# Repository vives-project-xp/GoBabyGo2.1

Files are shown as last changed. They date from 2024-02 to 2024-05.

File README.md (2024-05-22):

# GoBabyGo2.1

## About

Go Baby Go 2.1 is an innovative project that aims to enhance the mobility and independence of children with disabilities.
This project was created as part of the Project Experience course at [VIVES University of Applied Sciences](https://www.vives.be/en), in collaboration with the Ergotherapy program. This project focuses on adapting mini-cars to meet the specific needs of these children.
The main goal of this project is to create a working product out of the previous proof of concept [GoBabyGo2.0](https://github.com/vives-project-xp/GoBabyGo2.0), where the functions of the steeringweel and the gaspedal are replaced by a joystick.
By creating adaptable vehicle kits and comprehensive instructions, the project strives to empower caregivers and non-technical individuals to customize cars for children with ease.

## The team

- [Alberiek Depreytere](https://github.com/AlberiekDepreytere): Supervision, assembly, architectural design,...
- [Vic Verbiest](https://github.com/Vic-Verbiest): methodologie, bestellingen, 3d prints
- [Lynn Delaere](https://github.com/LynnDelaere): Maintain documentation and support developers

## Features

- Assembly kit development
- Comprehensive manual
- Implementing joystick as steering
- Standalone with interference from controller

## How it works

The project focusses on developing a user-friendly assembly kit with easy to follow instructions for converting standard mini-cars into accessible vehicles for children with disabilities. The function of the steering wheel and accelerator pedals are replaced by a joystick.
The assembly kit comes with easy to follow instructions so the assembly kit can be made and added to the package of the car. Every car comes then with a conversion manual so the assembly kit can easily be installed on the car. The assembly kit is engineered with user-friendly design principles, ensuring accessibility for individuals without prior experience in electronics.

## Project status

The ride-on car has been successfully converted to a ride-on car with a joystick, a guide on how to make the assembly kit has been made and an installation manual had been written out.

## Documentation

The documentation folder contains an [assembly kit](/Documentation/Manuals/Handleiding%20ombouwkit.md) and an [installation manual](/Documentation/Manuals/Installatie%20ombouwkit.md) to convert a ride-on car.

//Last updatet 13/05/2024 09:00 CET

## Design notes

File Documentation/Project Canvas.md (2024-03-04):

# Project Canvas

## Purpose and goal

Make an assembly kit for a ride on car with a joystick.

## Scope

In this project, we need to modify a ride-on car to utilize a joystick instead of a steering wheel. This includes providing an easy-to-follow manual so that everybody can convert the ride-on car if necessary.

## Succes Criteria

This project will be a succes if we can create an easy assembly kit to modify the ride-on car.

## Milestones

- Week 1-3: developing concept and order list
- Week 4-6: devoloping a prototype
- Week 7-10: final product/ proof of concept
- Week 11-12: debugging and optimizing
- Week 13: presentation

## Actions

- Electronic diagram ride-on car
- Order list
- Testing joystick
- Measuring hardware
- 3D print to attach joystick
- Instruction manual
- Keeping GitHub up to date

## Team

- Alberiek Depreytere: Hardware engineer, Scrum master
- Vic Verbiest: ***AANVULLEN***
- Bavo Lezy: ***AANVULLEN***
- Lynn Delaere: Administration and communication

## Stakeholders

- Occupational therapy
- Project leader
- Parents of children with a disabilitie

## Users

Children with a disabilitie

## Resources

- Github repository
- Financial budget €175
- Lab equipment
- Input occupational therapy

## Constraints

- Financial budget
- Time (13 weeks)

## Risks

- Hardware not compatible with eachother
- Long-term absent team member
- Too complex conversion kit
- Loss of documentation

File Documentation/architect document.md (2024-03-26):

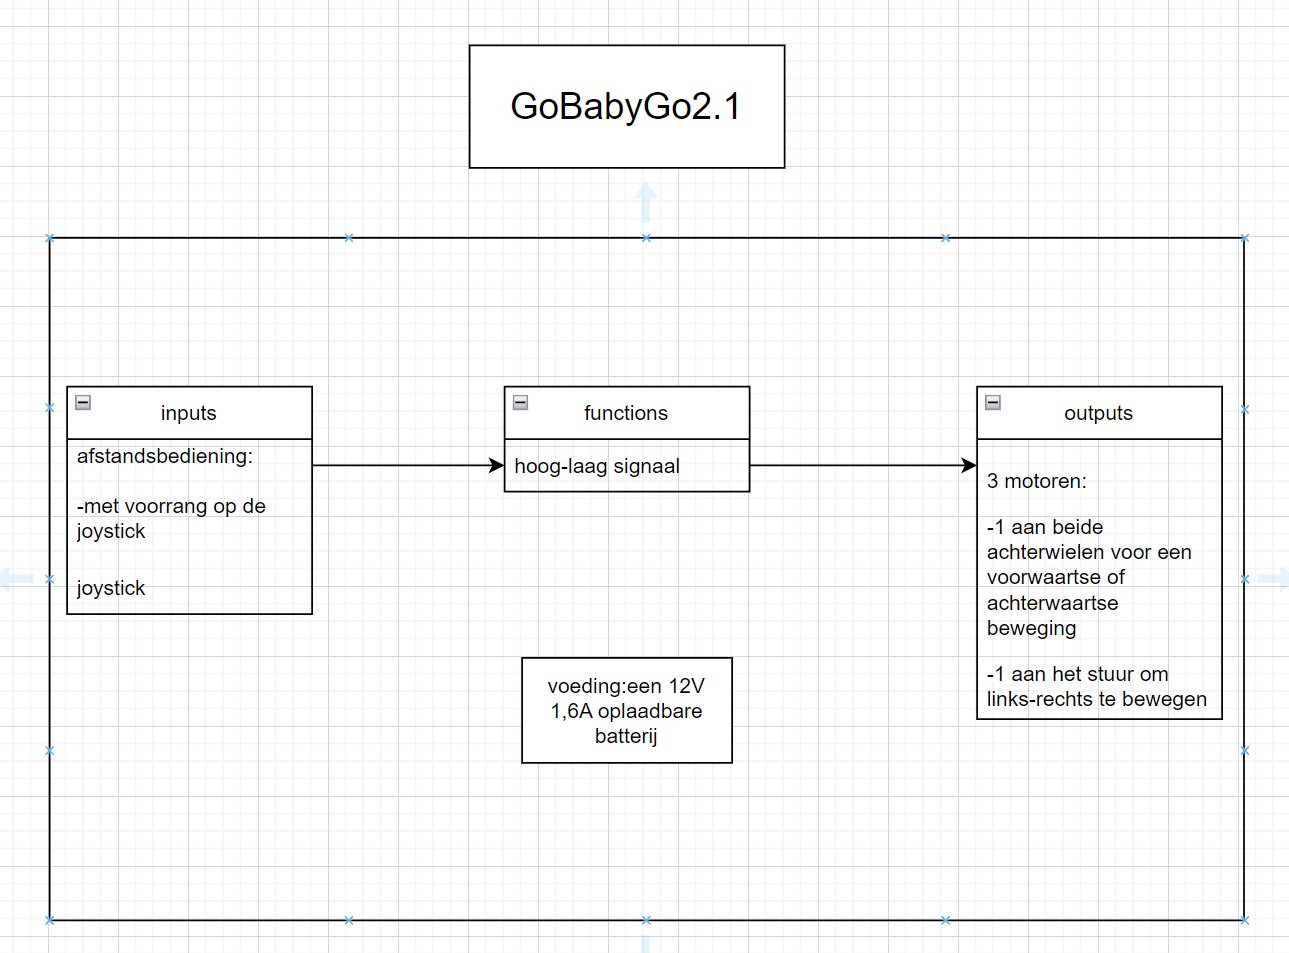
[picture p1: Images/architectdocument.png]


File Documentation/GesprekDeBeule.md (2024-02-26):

# Gesprek Isabelle De Beule
## Vragen Auto
Hebben jullie nog een originele auto zonder modificaties?
> Er Zijn nog 5 originele auto's Er zijn nog 5 originele auto’s aanwezig in campus Kortrijk in het zorglab. Er word een auto overgebracht zodat we een elektrisch schema kunnen opstellen aan de hand van een nieuwe auto. Aan de hand van een originele auto wordt eveneens de ombouwkit opgesteld.

Zijn de auto's allemaal van hetzelfde type?
> De auto’s die worden aangekocht zijn telkens van het merk Mercedes en hetzelfde model.

Waar werden de auto's aangekocht, welk model werd er aangekocht en wie is de fabrikant van de auto's?
> Bij [atoys](https://www.atoys.nl/webshop/verwacht/detail/1122/mercedes-benz-glc-63-elektrische-accu-auto-met-muziek-module-en-meer-1.html) worden de auto’s in bulk aangekocht, het model die telkens wordt besteld is de Mercedes Benz GLC 63

Wie heeft de modificaties uitgevoerd met de drukknop? Kunnen wij deze persoon in kwestie contacteren.
> De modificaties werden uitgevoerd door de studenten van zorgtechnologie onder begeleiding van de docent. Deseine Bert is de docent in kwestie. De voetpedaal werd enkel vervangen door een drukknop op het stuur.

## Vragen joystick
Hoeveel ruimte moet er vrijgehouden worden voor de plaatsing van de stoel?
>De joystick mag in de plaats komen waar het stuur zich nu bevind. Zo is er nog plaats om een aangepaste stoel te plaatsen indien nodig. Als de joystick te veel naar voor komt, is het moeilijker om een aangepaste stoel te plaatsen.

Hoe hoog mag de joystick komen?
>Doordat de joystick in de plaats komt van het stuur is dit geen probleem met hoogte. Maar veel hoger mag dit ook niet komen.

Moet dit een speciale joystick zijn of is deze die er momenteel inzit goed genoeg?
> Dit mag een standaard joystick zijn met niet te veel snufjes zodat de kindjes hierdoor geen extra prikkels krijgen.

Moet er nog iets van het dashboard werken?
> De muziek van het dashboard mag nog werken, er mag ook een optie in de kit aanwezig zijn dat dit er uit gehaald kan worden.
De startknop mag weg zodat de kindjes minder prikkels heeft en zich enkel kan focussen op de joystick.
De wielen aan de onderkant moeten blijven zitten zodat de ouders de auto nog kunnen voor uittrekken.
Er zijn enkele problemen met de batterij. Dit tijdens het opladen, de killswitch moet aan staan vooraleer de batterij kan opgeladen worden. Hier zullen we kijken of er een mogelijkheid is dat de batterij toch oplaad ongeacht de stand van de killswitch. Ook de levensduur van de batterij is een probleem, na 30-45 minuten rijden is de batterij plat. We houden de optie open om een zwaardere batterij te gebruiken die compatibel is met de schakeling die we zullen gebruiken.

## Extra info
Bert Deseine - docent elektronica in de opleiding zorgtech (handleiding)
Benjamin Van Der Smissen - docente project in de opleiding zorgtech
Sofie Vanmaercke - OH zorgtech

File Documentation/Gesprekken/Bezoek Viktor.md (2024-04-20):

# Bezoek Viktor 15/04/2024

Op 15/04/2024 kwam Viktor langs om een testrit uit te voeren met ons prototype. Viktor is het kindje die geselecteerd werd door ergotherapie en komt in aanmerking voor een ride on auto met joystick. Viktor rijd thuis regelmatig rond met een rolstoel met joystick dus bekend met het gebruik van een joystick.
Tijdens de testrit werd de werking van de ombouwkit geëvalueerd en de plaatsing van de joystick.
Over de werking van de schakeling is niets op aan te merken, de auto rijdt vooruit, achteruit, links en rechts wanneer de joystick deze richting geduwd wordt. De joystick is minder gevoelig dan de joystick dat Viktor gewent is. Dit komt deels doordat de constructie waarin de joystick zit wat wankel staat.
De werking van de schakeling is niets op aan te merken behalve dat de joystick die wordt gebruikt minder gevoelig is dan de joystick die Viktor gewoon is. Dit komt deels doordat de constructie van de 3D prints waar de joystick inzit niet stabiel staat. Dit wordt bekeken en de 3D prints worden aangepast waar nodig.
De plaatsing van de joystick werd zowel door de ouders van Viktor als ergotherapie goedgekeurd. In samenspraak met de ouders, ergotherapie en de projectcoaches werd er beslist om geen extra ondersteuning te voorzien voor Viktor zijn armpjes. Voor Viktor is dit een extra motivatie om zijn armpjes te strekken om zo goed de auto te besturen. Wel kan ergotherapie ervoor zorgen dat de zitschaal waar Viktor inzit wat naar voor geplaatst kan worden.

Hier zijn enkele foto's en een filmpje van Viktor in de auto.
<!--foto's toevoegen-->

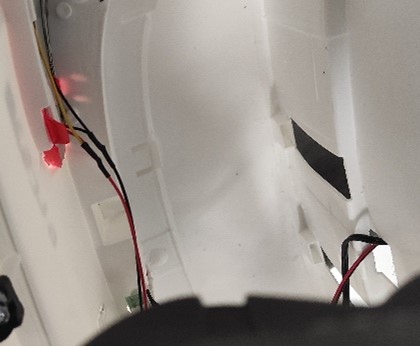
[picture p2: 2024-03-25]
Images/Draad_Doorsteken.jpg

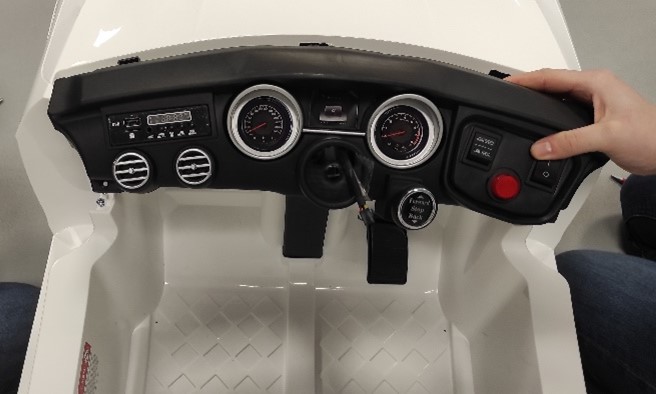
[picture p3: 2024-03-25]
Images/Dashboard_Afhalen.jpg

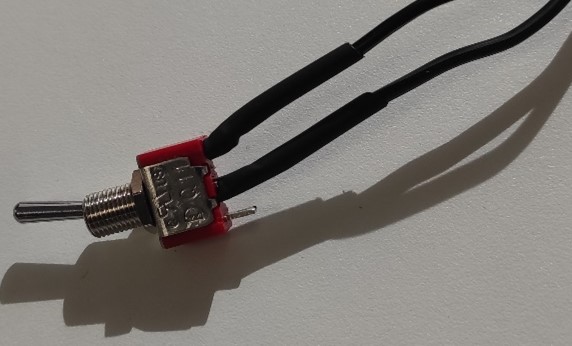
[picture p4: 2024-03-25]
Images/Killswitch_schakelaar.jpg

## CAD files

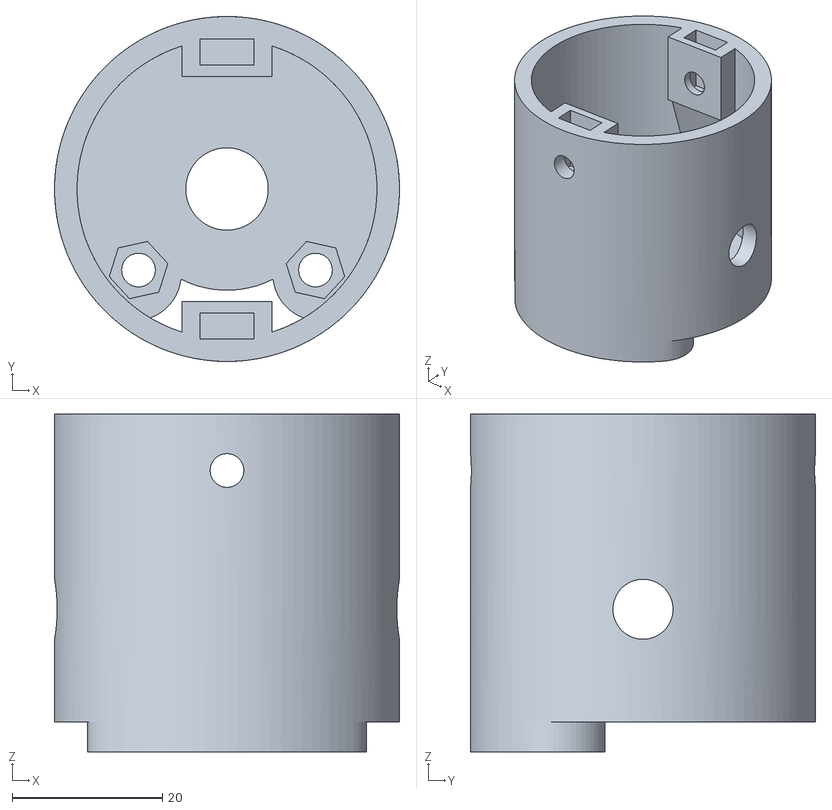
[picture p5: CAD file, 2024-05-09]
Documentation/Final Design 3D Prints/KoppelstukDashboard.stl
46.0 x 46.0 x 45.0

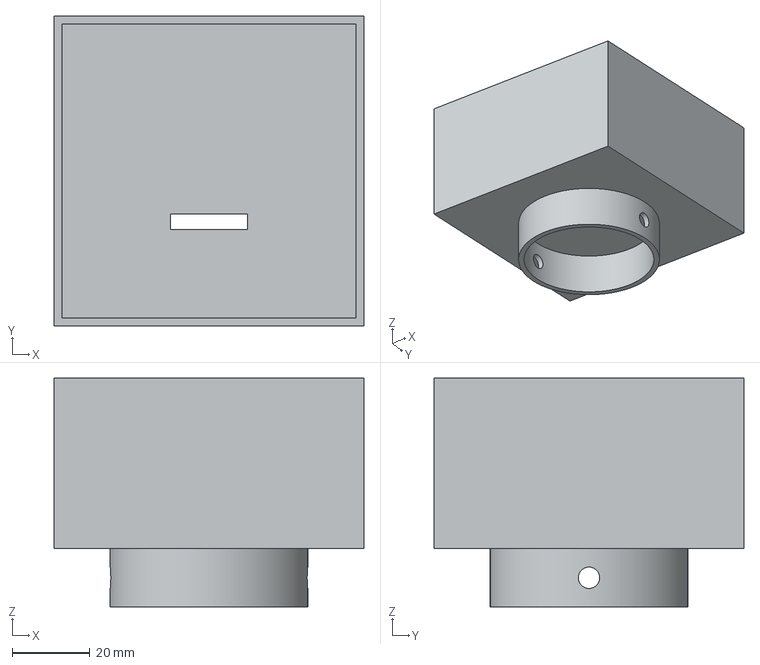
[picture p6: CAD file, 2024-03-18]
Documentation/Test Design 3D Prints/joystick.3mf
80.0 x 80.0 x 59.0 mm

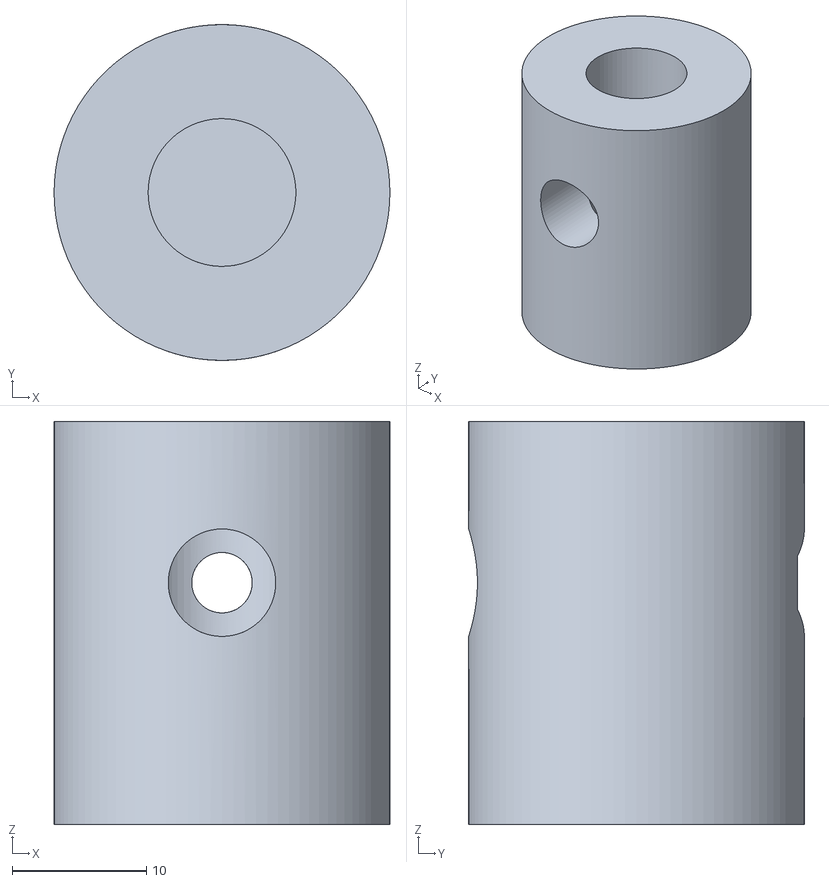
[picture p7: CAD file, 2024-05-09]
Documentation/Final Design 3D Prints/StuurStangHouder.stl
25.0 x 25.0 x 30.0

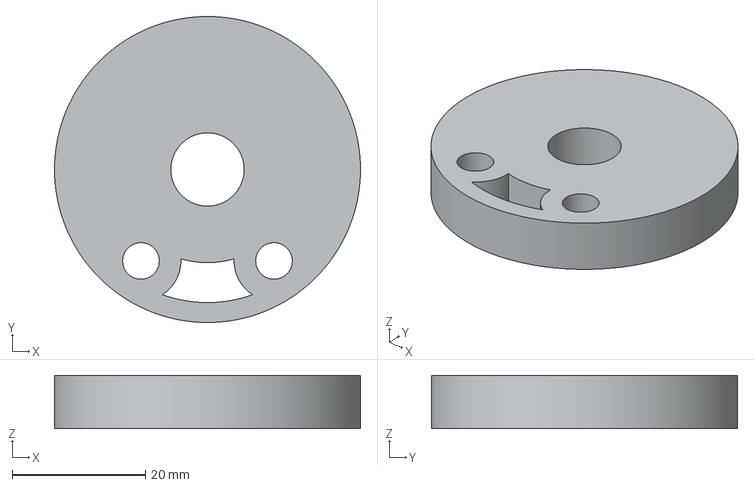
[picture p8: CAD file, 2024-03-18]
Documentation/Test Design 3D Prints/joystickhouderhouder.3mf
46.0 x 46.0 x 8.00 mm

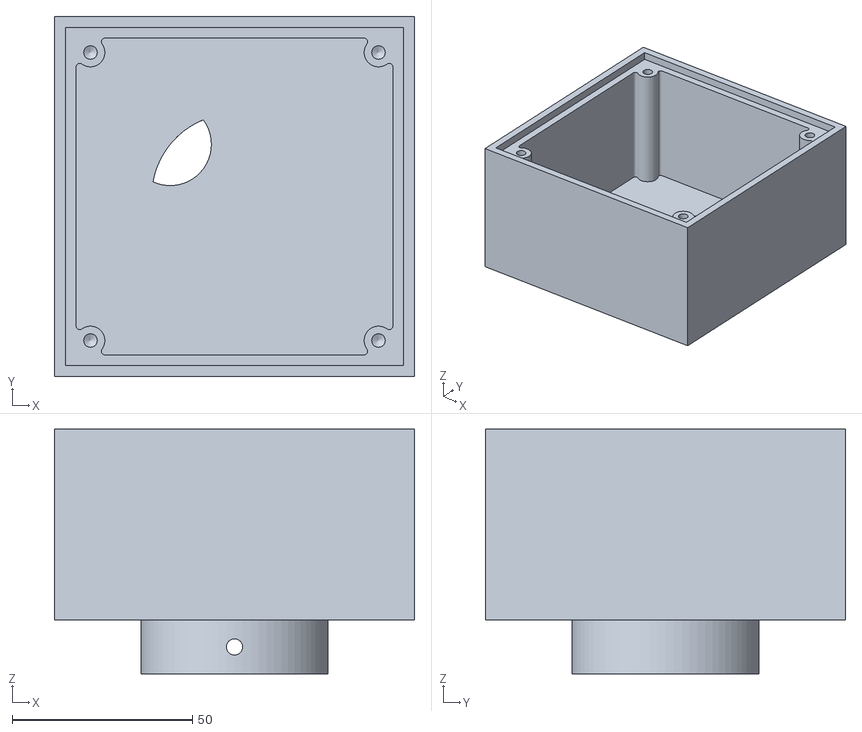
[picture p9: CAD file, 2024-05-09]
Documentation/Final Design 3D Prints/DoosJoystick.stl
100.0 x 100.0 x 68.0

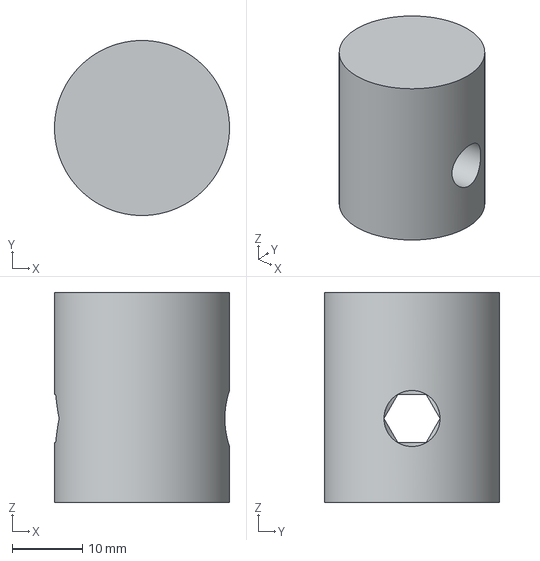
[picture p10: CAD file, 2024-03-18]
Documentation/Test Design 3D Prints/stanghouder.3mf
25.0 x 25.0 x 30.0 mm

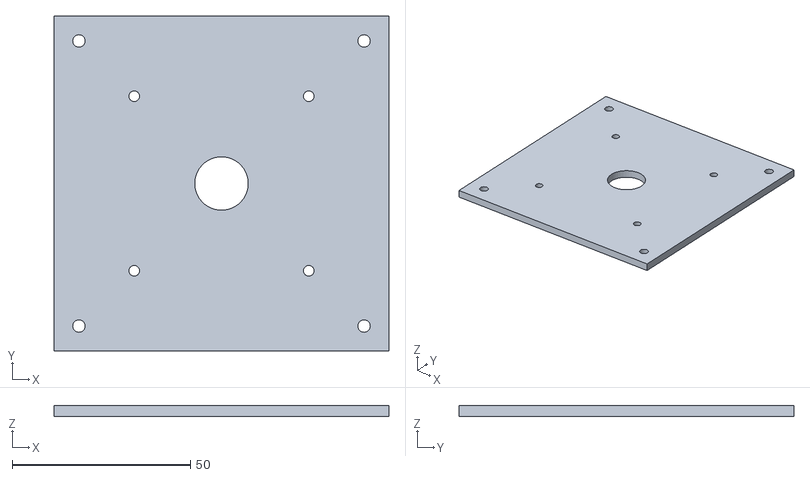
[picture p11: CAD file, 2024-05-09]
Documentation/Final Design 3D Prints/DekselDoos.stl
94.0 x 94.0 x 3.00

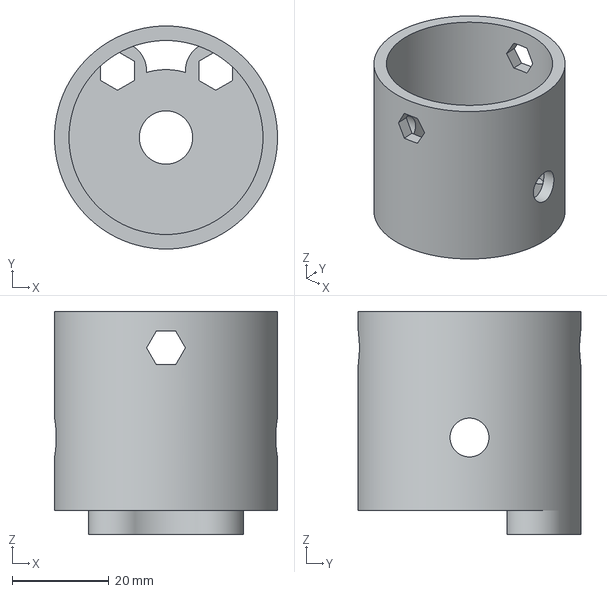
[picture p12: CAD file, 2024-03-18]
Documentation/Test Design 3D Prints/joystickhouder.3mf
46.0 x 46.0 x 46.0 mm

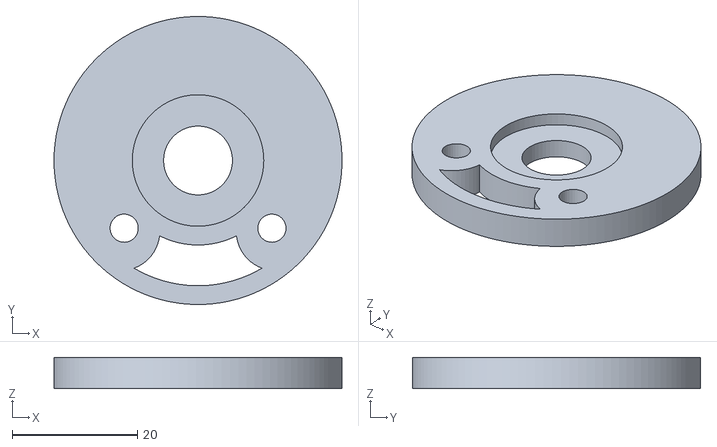
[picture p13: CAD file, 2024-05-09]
Documentation/Final Design 3D Prints/SpanStukDashboard.stl
46.0 x 46.0 x 5.00

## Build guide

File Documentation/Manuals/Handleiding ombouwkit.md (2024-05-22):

# Handleiding ombouwkit

## Inhoud

* [Opmerking](#opmerking)
* [Onderdelen](#onderdelen)
* [Materiaal](#materiaal)
* [Tools](#tools)
* [Handleiding](#handleiding)

## Opmerking

Deze ombouwkit is ontworpen voor een specifieke elektrische kinderauto van het type Mercedes-Benz GLC63, met productcode QLS5688-grey.

## Onderdelen

Hieronder vind je een lijst van de verschillende onderdelen die nodig zijn om de ombouwset te maken, de leveranciers van de onderdelen alsook een woordje uitleg over de onderdelen.

### Joystick

De joystick die gebruikt dient te worden is van het merkt Joy-IT, deze heeft 4 microschakelaars om de richting door te geven en springt automatisch terug naar de middenpositie. Deze is te verkrijgen bij de leverancier Conrad via deze [link](https://www.conrad.be/nl/p/joy-it-arcade-joystick-professional-8-invoerapparaat-geschikt-voor-arduino-banana-pi-cubieboard-pcduino-raspberry-p-1555268.html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).

### 3D onderdelen

Er zijn 5 verschillende 3D stukken nodig om de joystick vast te zetten op het dashboard van de auto, een doos om de joystick in weg te steken, een deksel om dit af te sluiten, een koppelstuk tussen het dashboard en de doos, een stuk die de stuurstang omhoog houdt en een stuk die dit alles vastzet aan de onderkant van het dashboard. In de map [3D-prints](../3D-prints/) vind je de verschillende onderdelen terug die zullen afgedrukt moeten worden.

### Motor driver

De links-rechtssturing wordt bepaald aan de hand van de motor die aanwezig is op de stuurstang in de auto. Via de driver wordt de richting van de motor bepaald deze is een L298N driver, te verkrijgen bij Otronic via deze [link](https://www.otronic.nl/nl/l298n-motor-driver-board-rood.html). [Datasheet L298N](DatasheetL298_H_Bridge.pdf)
De L298N is een dubbele H-brug-motordriver die de snelheid en de richting van twee DC-motoren tegelijk mogelijk maakt, in ons geval moeten we maar één motor aansturen. De module kan een DC-motor aansturen met een spanning tussen de 5 en 35V en een piekstroom van 2A.

Er zijn twee schroefklemmenblokken aanwezig respectievelijk voor motor A en motor B, een schroefklemblok voor de aarding, de Vcc voor de motor en een 5V-pin die zowel een ingang als een uitgang kan zijn, dit bijvoorbeeld voor een microcontroller. Er zijn 6 control pins aanwezig, pin 1 en 6 dienen om de snelheid van de motoren te regelen met behulp van een microcontroller, pinnen 2 en 3 dienen om de draairichting van motor A te regelen en pinnen 4 en 5 om de draairichting van motor B te regelen.

In ons geval zullen we enkel pinnen 2 en 3 gebruiken om de draairichting van de motor te regelen. Met de pinnen van de draairichting besturen we de schakelaars van de motor driver, als ingang 1 laag is en ingang 2 hoog, zal de motor vooruit bewegen, omgekeerd, als ingang 1 hoog is en ingang 2 laag is zal de moto achteruit bewegen. Als beide ingangen hetzelfde zijn, laag of hoog, zal de motor stoppen.

De L298N zorgt voor een spanningsval van ongeveer 2V, hierdoor zal de spanning op de motorklemmen ongeveer 10V zijn, wat betekent dat we niet de maximale snelheid uit de 12V DC-motor kunnen halen.

### Tuimelschakelaar

De auto wordt voorzien van een kill-switch om de stroom naar beide motoren te onderbreken.
Deze tuimelschakelaar is te verkrijgen bij de leverancier Conrad via deze [link](https://www.conrad.be/nl/p/tru-components-1587664-tc-r13-2-05-tuimelschakelaar-250-v-ac-1-5-a-1x-uit-aan-continu-1-stuk-s-1587664.html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).

## Materiaal

In de onderstaande lijst, staat het nodige materiaal om de ombouwset te maken.

* 3 x 140cm rode h05v-k flexibele koper kabel van ø 1.5mm²  = 420 cm
* 7 x 20cm rode h05v-k flexibele koper kabel van ø 1.5mm²  = 140 cm
* 3 x 30cm zwarte h05v-k flexibele koper kabel van  ø 1.5mm² = 30cm
* 9 x Wago verbindingsklem 3-voudig  geschikt voor geleiders met maximale doorsnede van 4mm²
* 8 x Kabelschoenen (Indien je een ander type joystick gebruikt controleer steeds dat de kabelschoenen passen naar behoren.)
* 2 x Female jumper connector dupont (krimp uitvoering)
* 5 x Moeren maat M5
* 5 x Metaalschroeven maat M5
* 4 x Schroefdraadbussen M3
* 4 x Metaalschroef M3 30mm

## Tools

Volgende tools zijn nodig om de ombouwset in elkaar te monteren.

* Platte kop schoevendraaier
* Kruiskop schroevendraaier
* (Zij)Kniptang
* Striptang (Best een instelbare voor de verschillende diameters.)
* Soldeerbout
* Soldeermat
* Soldeertin (Eventueel Flux)
* Krimptang
* Labels om kabels te labelen

## Handleiding

### Stap 1: 3D-prints joystick

Plaats de 4 schroefdraadbussen maat M3 in de daarvoor bestemde gaten van de 3D-print waar de joystick wordt geplaatst.
Plaats de 4 schroefdraadbussen maat M3 in de daarvoor bestemde gaten van de 3D-print waar de joystick wordt geplaatst.
Gebruik hiervoor een soldeerbout om het plastic voorzichtig te laten smelten.
Zorg ervoor dat de soldeerbout een dikke punt heeft en ingesteld is op ± 200°C.
Wacht even totdat de warmte gelijkmatig wordt verdeeld en smelt de schroefdraadbus voorzichtig in het plastic.
Doe hetzelfde voor de stuurstanghouder waar een uitsparing is voorzien voor een M5-moer.
Plaats 2x M5-moeren in de daarvoor voorziene plaats van het dashboard koppelstuk en schuif 2x M5-moeren in de voorziene gleuven van het dashboardkoppelstuk.

Schroef de metalen plaat die standaard aan de joystick hangt los en bevestig in plaats daarvan het deksel voor de doos aan de joystick met de bijbehorende schroeven.
Schroef de metalen plaat die standaard aan de joystick hangt los en bevestig in plaats daarvan het deksel voor de doos aan de joystick met de bijbehorende schroeven.
Schroef de groene stukken onderaan de joystick los, deze zijn niet nodig.

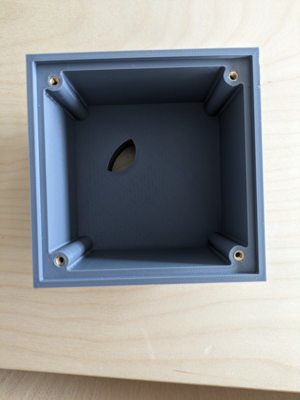
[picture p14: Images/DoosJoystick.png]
Doos joystick Doos met alle schroefdraadbussen


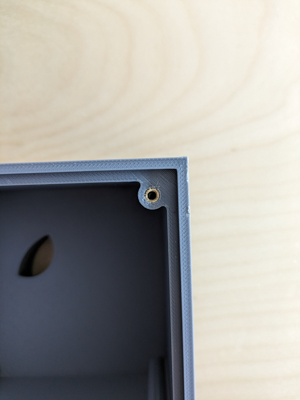
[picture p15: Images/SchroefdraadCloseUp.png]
Schroefdraadbussen doos Close-up schroefdraadbussen


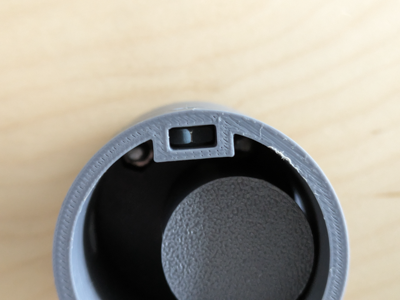
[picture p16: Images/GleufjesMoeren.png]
Gleuf voor moer Gleuven voorzien voor moeren


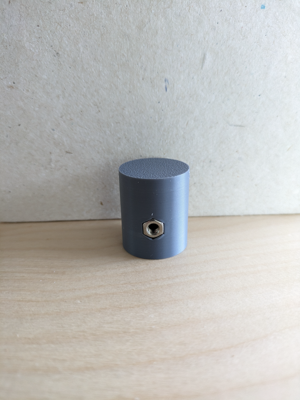
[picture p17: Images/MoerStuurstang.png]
Moer stuurstang Vastgezette moer stuurstang


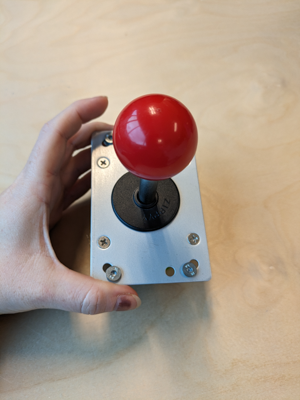
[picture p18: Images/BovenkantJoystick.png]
Bovenkant joystick Bovenkant joystick met metalen plaat


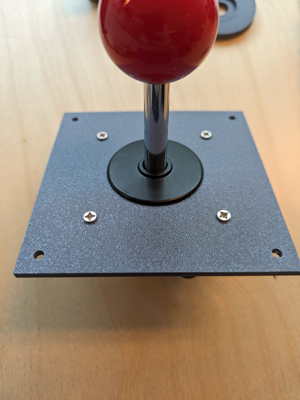
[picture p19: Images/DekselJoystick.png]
Deksel met joystick Deksel voor de doos op de joystick


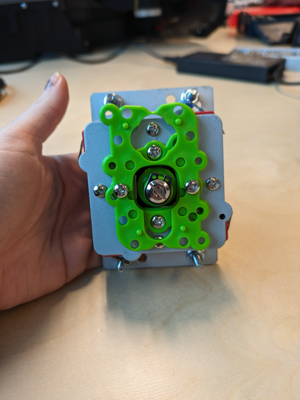
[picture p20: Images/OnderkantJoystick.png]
Onderkant joystick Onderkant joystick groene stukken voor richtingbepaling


### Stap 2: Voorbereiding bekabeling

Knip 3 rode kabels van ±140cm lang en 7 kabels van ± 20cm lang.
Knip 3 zwarte kabels van ± 20cm lang.
Ontmantel alle kabels zodat ±1cm isolatie van de draad verwijderd is.

Bevestig een female jumper connector aan het uiteinde van 2 lange rode flexibele kabels en plaats ze in een plastic pin behuizing met behulp van de krimptang.
Vertin het andere uiteinde en bevestig hier kabelschoentjes aan. Label de 2 kabels met respectievelijk links en rechts.
Vertin beide uiteinden van de laatste lange rode kabel en plaats op één uiteinde een wago-connector. Label deze kabel met 5V.

Vertin alle uiteinden van de 7 stukken rode kabel. Bevestig kabelschoentjes aan 2 korte rode kabels en vertin het ander uiteinde.
Plaats deze 2 rode kabels samen met de lange rode kabel in een wago-connector.
Label deze 2 kabels met respectievelijk vooruit en achteruit.

Vertin alle uiteinden van de 3 korte zwarte kabels en bevestig kabelschoentjes aan 2 van deze kabels. Plaats twee kabels samen in een wago-connector.

**Opmerking:**
Als alternatief voor het vertinnen van de koperen kabels kan ook een adereindhuls gebruikt worden.

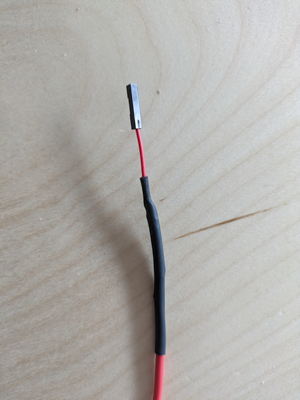
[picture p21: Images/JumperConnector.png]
Jumper connector uiteinde Twee jumper connectors


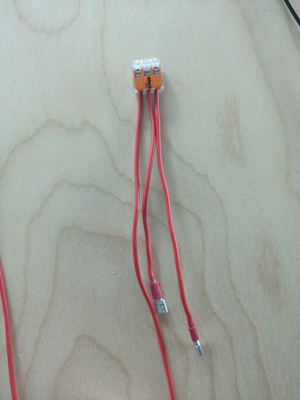
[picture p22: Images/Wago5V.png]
5V connector Wago om de 5V door te lussen


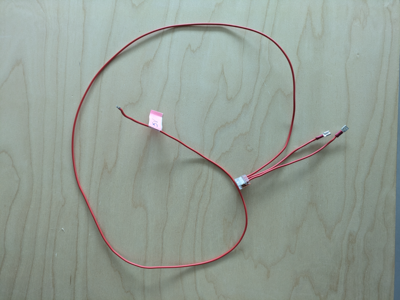
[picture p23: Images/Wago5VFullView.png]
5V connector full view Wago om de 5V door te lussen


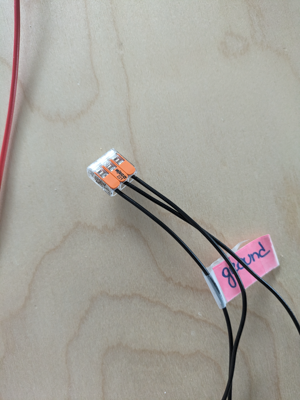
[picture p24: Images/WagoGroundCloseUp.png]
Ground connector Wago om de ground door te lussen


### Stap 3: Verbinding motor driver

Verbind 3 korte rode kabels met de motordriver respectievelijk met OUT1, OUT2 en +12V verbind alle uiteinden van de kabels met een wago.

Verbind 1 korte zwarte draad met de motordriver respectievelijk met GND en verbind het uiteinde van de draad met een wago.

Verbind de 5V kabel met de 5V pin op de motordriver.

Verbind de linkse gelabelde kabel met de IN1 en de rechts gelabelde kabel met de IN2.

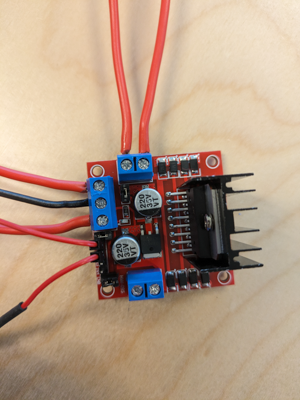
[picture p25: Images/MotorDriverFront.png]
Bovenkant motordriver Bovenaanzicht motordriver


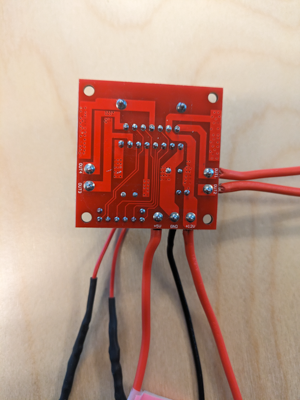
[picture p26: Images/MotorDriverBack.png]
Onderkant motordriver Onderaanzicht motordriver


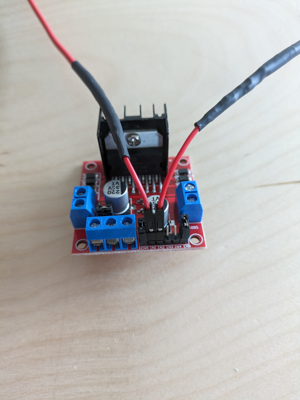
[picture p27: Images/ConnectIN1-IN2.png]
Pin aansluiting jumper connector Vooraanzicht motordriver


### Stap 4 Kill-switch maken

Knip 1 rode kabel van 1m40 lang en 1 zwarte kabel van 1m40 lang.
Ontmantel beide kabels zodat ongeveer 1cm van de isolatie verwijderd is, vertin één kant van de beide kabels en maak de vorm van een haakje, vertin het andere uiteinde.
Vijs de haakjes die gemaakt werden vast aan de kill-switch en plaats op het andere uiteinden van de rode en zwarte draad een wago.

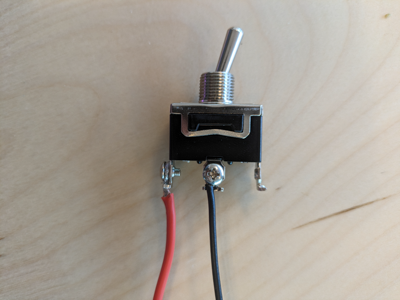
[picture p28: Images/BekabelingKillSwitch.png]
Aansluiting kill-switch Aansluiting kabels killswitch


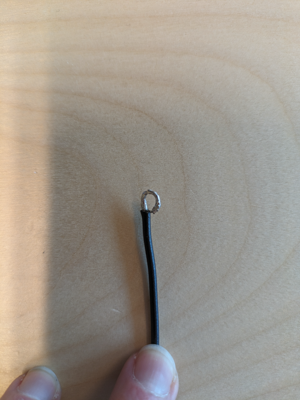
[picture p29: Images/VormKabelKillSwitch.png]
Vorm koper draad Vorm haakje koper draad


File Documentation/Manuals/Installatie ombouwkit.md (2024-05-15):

# Installatie ombouwkit

## Inhoud

* [Opmerking](#opmerking)
* [Benodigdheden](#benodigdheden)
* [Installatie](#installatie)
  * [Auto uitpakken](#auto-uitpakken)
  * [Batterij testen](#batterij-test)
  * [Kill-switch](#kill-switch)
  * [Ombouwkit](#ombouwkit)
  * [Joystick en 3D prints](#joystick-en-3d-prints)
  * [Deuren en spiegels](#deuren-en-spiegels)
  * [Wielen](#wielen)

## Opmerking

Deze ombouwkit is ontworpen voor een specifieke elektrische kinderauto van het type Mercedes-Benz GLC63, met productcode QLS5688-grey.

## Benodigdheden

Zorg dat je alle benodigdheden hebt voor je start aan het bouwen van de auto. In de hieronder bijgevoegde lijst vind je de benodigdheden:

* Ombouwkit
* 3D-prints
* Een aantal schroevendraaiers (plat en kruis)
* Kniptang
* Striptang
* Kabelbinders
* Joystick
* Boormachine

## Installatie

### Auto uitpakken

Haal de auto uit de verpakking en organiseer de inhoud per categorie.
Berg alle spullen netjes op om ervoor te zorgen dat er niets verloren gaat.
Positioneer de auto zodanig dat de voorkant aan je rechterzijde staat.
Deponeer het afval in de daarvoor bestemde vuilnisbak.
Het stuur is in dit geval niet meer nodig.

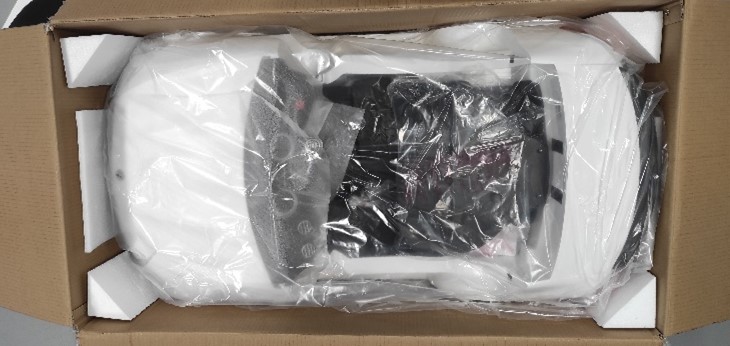
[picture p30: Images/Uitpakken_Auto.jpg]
Uitpakken auto Auto in doos


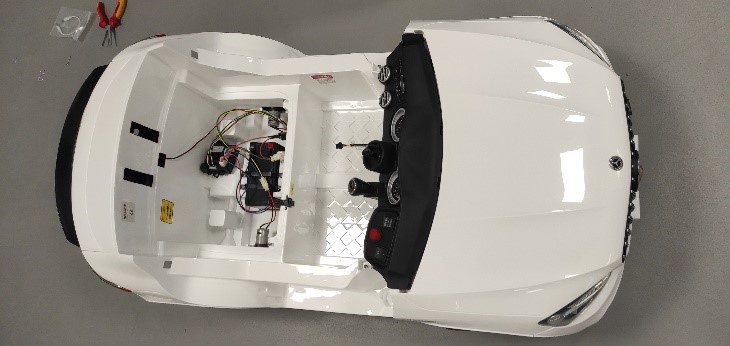
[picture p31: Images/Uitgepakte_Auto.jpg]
Uitgepakte auto


### Batterij test

Aan de linker zijde van de auto bevind zich de hoofdbekabeling van de auto.
In deze bak vind je de batterij, die nog niet is aangesloten.
Aan de powersocket bevind er zich een rode kabel en een zwarte kabels.
Sluit de rode kabel aan op het rode klepje van de batterij, de zwarte kabel op het zwarte klepje van de batterij.
Test of de batterij goed is aangesloten door de auto aan te zetten.
Koppel de batterij terug los nadat je deze hebt getest, zo kan er veilig gewerkt worden.  

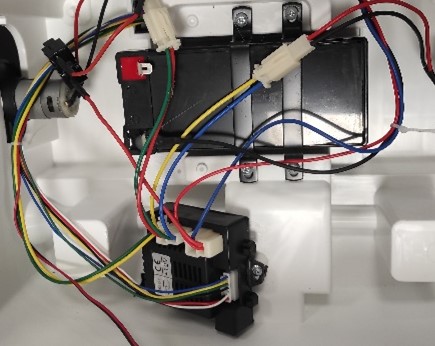
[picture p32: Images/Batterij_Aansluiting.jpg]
Batterij Hoofdbekabeling


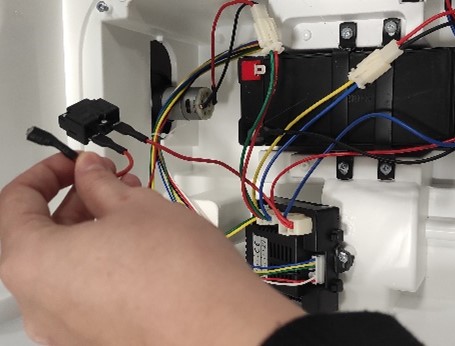
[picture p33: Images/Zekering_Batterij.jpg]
Zekering batterij Aansluiting zekering op batterij


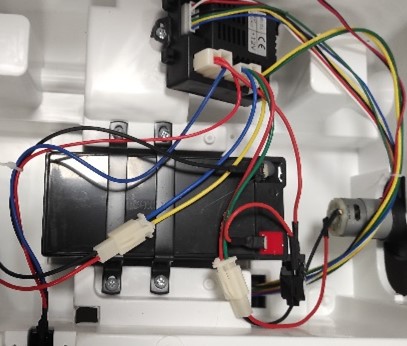
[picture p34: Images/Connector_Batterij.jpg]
Aangesloten batterij Aansluiting batterij


### Kill-Switch

Verwijder het gaspedaal voorzichtig uit de auto en maak de kabelschoentjes los die eraan vast zitten.
Verwijder ongeveer 1cm van de isolatie van de beide paarse kabels, vertin de uiteinde van beide kabels of plaats een adereindhuls op de kabels.
Stop beide kabels in de wago samen met de kill-switch.

Plaats de wago's terug in de opening van de gaspedaal en leid de kabels en de kill-switch door de opening naar de onderkant van de auto. Maak de kabelgoot aan de onderkant van de auto los en leg de kabels van de kill-switch erin, richting de achterkant van de auto. Bind de kabels van de kill-switch vast met een paar kabelbinders. De kabelgoot dient voorlopig niet dicht gemaakt te worden. Haal de kabels van de kill-switch door de opening waar alle andere kabels lopen. Steek de kabels en de kill-switch door de opening voorzien voor de achterlichten.

Boor een gat in de achterkant van de auto om de kill-switch te plaatsen. Zorg ervoor dat het gat niet te dicht bij de rand van de auto zit zodat dit makkelijk bereikbaar is vanaf de onderkant. Steek de kill-switch door het gat en schroef deze vast met de meegeleverde moer.

Tip: Het is ook steeds handig om de kill-switch met de On-kant naar boven de plaatsen. Op deze manier moet je enkel naar beneden duwen voor de auto uit te zetten.

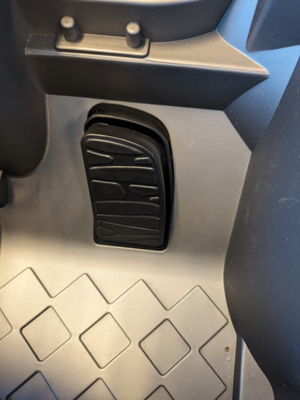
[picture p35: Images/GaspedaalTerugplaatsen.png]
Gaspedaal Gaspedaal auto


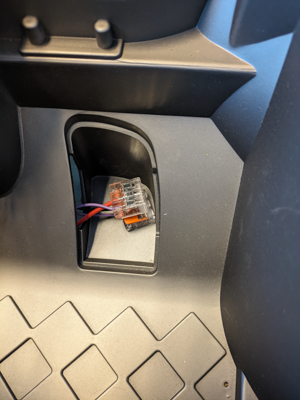
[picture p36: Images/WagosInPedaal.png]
Wago's onder gaspedaal


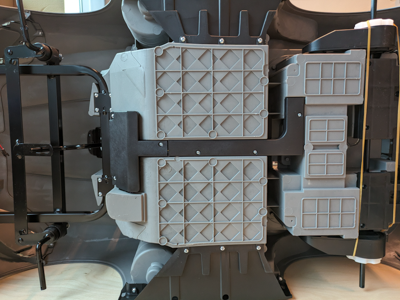
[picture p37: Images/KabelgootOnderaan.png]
Kabelgoot onderaan auto Onderaanzicht auto voor kabelgoten


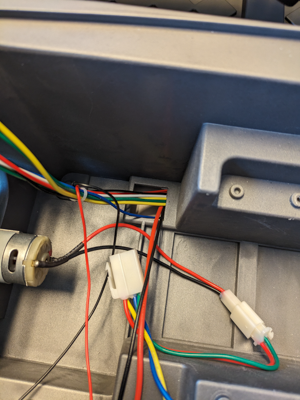
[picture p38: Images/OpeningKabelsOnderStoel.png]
Opening kabels onder stoel Opening voor kabels onder de stoel


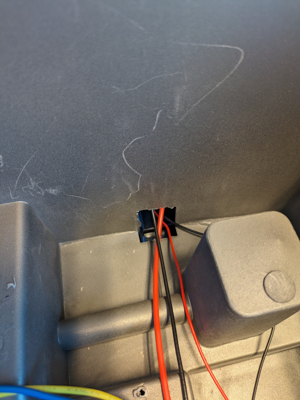
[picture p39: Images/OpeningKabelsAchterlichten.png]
Opening kabels voor achterlichten Opening voor kabels achterlichten


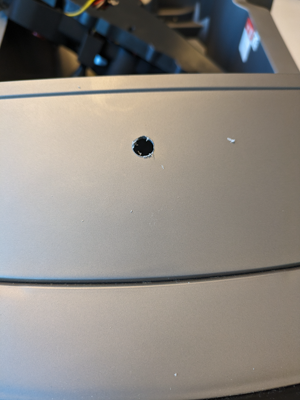
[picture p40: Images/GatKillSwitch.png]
Gat voor Kill-switch Gat voor kill-switch


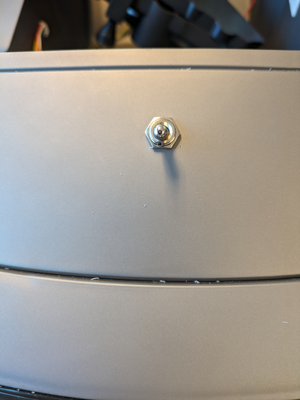
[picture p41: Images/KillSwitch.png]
Kill-switch Plaatsing kill-switch


### Ombouwkit

Leg de ombouwkit in de ruimte waar de batterij zich bevind.
Steek de kabels voor de joystick in de opening waar de andere kabels lopen, respectievelijk een kabel voor links, rechts en 5V.
Plaats deze kabels in de kabelgoot onderaan de auto naar voor.
Vijs de kabelgoot vooraan in de auto open en leg de kabels ook in deze kabelgoot.
Vijs het dashboard open, haal het voorzichtig van de stuurstang en haal de kabels van de ombouwkit voorzichtig door de opening waar de andere kabels doorlopen.

Lokaliseer de groene, paarse en gele draad die verbonden zijn met een kabelschoentje op de schakelaar om vooruit of achteruit te rijden.
Knip deze draden door en strip de draden zodat ±1cm van de isolatie verwijderd is.
Vertin de uiteinden van de draden of plaats een aderhuls over de draden.
Steek de groene draad in een Wago samen met de rode draad gelabeld met achterwaarts en de gele draad in een Wago samen met de draad gelabeld voorwaarts.
Plaats de paarse kabel samen in een Wago met de 2 zwarte korte kabels gelabeld ground.

Indien gewenst kunnen de overtollige draden van de audio interface verwijderd worden.
Dit zijn de draden die oorspronkelijk naar het stuur liepen. Dit zijn respectievelijk 3 draden, geel, zwart en rood.
Ook kunnen de speakers losgekoppeld worden indien gewenst, dit zijn de 2 gele draden.
De lampen van het dashboard kunnen ook losgemaakt worden indien gewenst, dit is een zwarte connector met respectievelijk één rode en één zwarte draad.

Opening kabels onder stoel Opening voor kabels onder de stoel

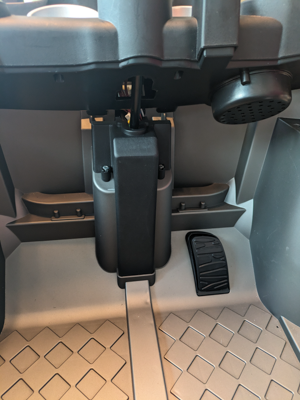
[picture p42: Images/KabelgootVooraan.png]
Kabelgoot vooraan dashboard Kabelgoot vooraan auto


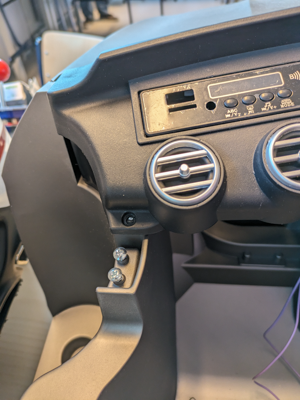
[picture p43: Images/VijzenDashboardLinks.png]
Dashboard links Vijs linkerkant dashboard


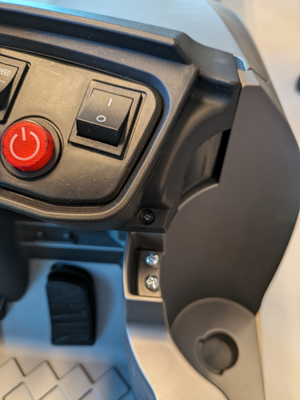
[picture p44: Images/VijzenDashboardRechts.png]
Dashboard rechts Vijs rechterkant dashboard


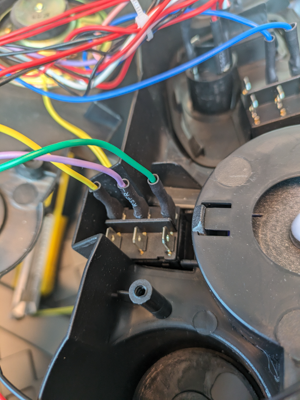
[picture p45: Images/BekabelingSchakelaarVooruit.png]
Bekabeling schakelaar vooruit/achteruit


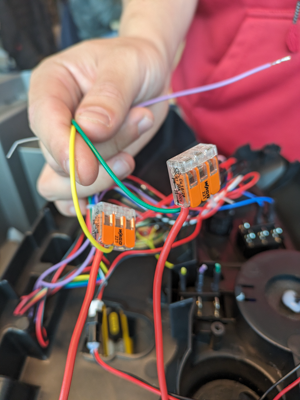
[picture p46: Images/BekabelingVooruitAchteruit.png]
Bekabeling joystick vooruit/achteruit


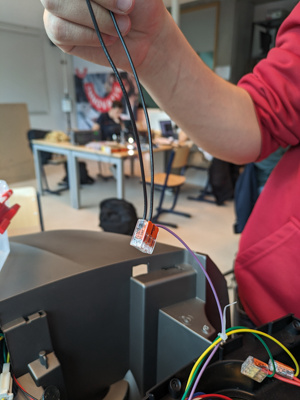
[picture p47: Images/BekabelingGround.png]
Bekabeling ground joystick


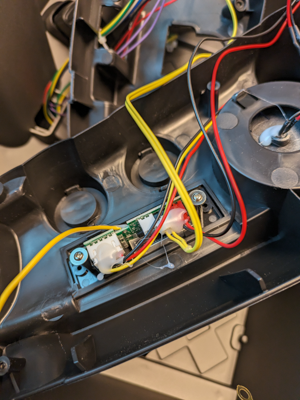
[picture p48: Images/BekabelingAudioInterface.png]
Bekabeling audio interface


Aan de achterkant van de auto lokaliseer je de groene en gele kabel die naar de motor driver van de auto lopen.
Koppel deze los en knip de connector van de draden af.
Strip de 2 draden zodat ongeveer 1cm van de isolatie verwijderd is en plaats de groene kabel samen in de wago die verbonden is met OUT1 en de gele kabel samen in de wago die verbonden is met OUT2.

Lokaliseer de zwarte kabel en witte kabel van de 7pin connector en knip deze door op ongeveer 5cm van de aansluiting op de motor driver.
Strip beide zijden van de draden.
Controleer of de draden die nog verbonden zijn met de 7pin connector lang genoeg zijn om verbinding te maken met de motordriver.
Indien dit niet het geval is, moet er een extra stuk draad worden toegevoegd met behulp van een kabelverbinder.
Zorg ervoor dat beide kabels goed verbonden zijn met elkaar.
Plaats de zwarte kabels samen in wago ground die zich op de motordriver bevind van de ombouwkit.
Plaats de witte kabels samen in de wago 12V op de motordriver.

Eens alles correct is geïnstalleerd kunnen de kabelgoten die los gemaakt werden terug vast gevezen worden.
Het dashboard wordt pas terug vast geplaatst tijdens het plaatsen van de 3D prints.

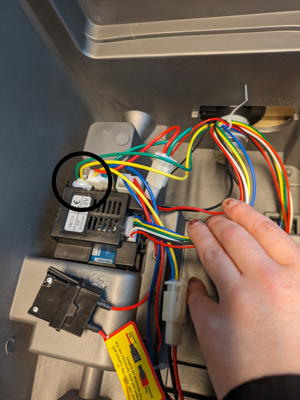
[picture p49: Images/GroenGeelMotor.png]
Groene en gele kabel motor Groene en gele kabels naar motor


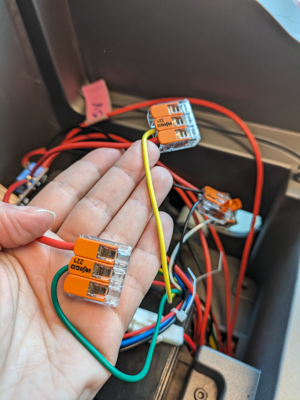
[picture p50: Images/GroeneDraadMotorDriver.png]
Groene draad motordriver Groene draad verbinden met OUT1


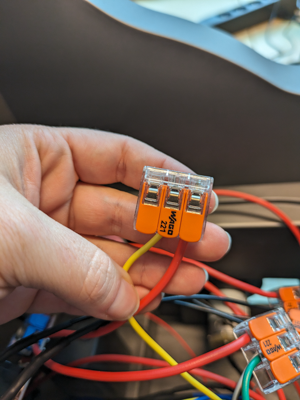
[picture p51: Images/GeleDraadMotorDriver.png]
Gele draad motordriver Gele draad verbinden met OUT2


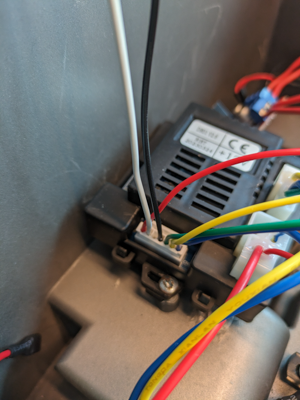
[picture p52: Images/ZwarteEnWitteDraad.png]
Zwarte en witte draad Zwarte en witte draad van 7pin connector


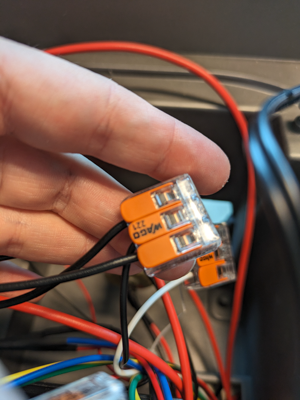
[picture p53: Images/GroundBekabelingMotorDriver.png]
Ground kabels wago Zwarte kabels voor ground


12V kabels wago Witte kabels voor 12V

### Joystick en 3D prints

Eens de ombouwkit volledig geïnstalleerd is, kunnen de kabels verbonden worden met de joystick om te testen of alles werkt. Indien alles correct werkt, kunnen deze terug losgekoppeld worden. Indien niet alles correct werkt, zal er ergens in de schakeling een slecht contact zijn of een fout met het verbinden van de correcte draden. Bekijk of alles correct is aangesloten, overloop of de installatie correct verlopen is.

Indien niet alles correct werkt, zal er ergens in de schakeling een slecht contact zijn of een fout met het verbinden van de correcte kabels.
Dit kan spanningsloos met een ohmmeter worden uitgemeten.

Plaats de ronde platte schijf (dashboard onderstuk) in de opening waar de stuurstang doorgaat en geleid de kabels naar de joystick hierdoor.
Steek eerst de kabels met de kabelschoentjes en vervolgens de overige kabels door de holte.
Indien nodig, verwijder tijdelijk de wago's van de kabels en plaats ze daarna terug.
Doe hetzelfde met de holle cilinder (koppelstuk dashboard).
Positioneer dit stuk in de uitkeping van het dashboard. Bevestig deze twee onderdelen aan elkaar met 2x M5-bouten. Zorg ervoor dat beide stukken stevig worden vastgezet, zodat deze niet kunnen loskomen of onstabiel zijn en speling hebben.

Leg de kabels over de cilinder, zodat de stuurstanghouder makkelijk geplaatst kan worden. Schuif de kleine cilinder (stuurstanghouder) over de stuurstang, en zorg ervoor dat de openingen in de 3D-prints zijn uitgelijnd met de openingen van de stuurstang. Bevestig de stuurstanghouder vast met een moer via de opening in de cilinder. Zorg ervoor dat de moer volledig door het 3D-print gaat, maar dat deze nergens aan kan haperen in de grote cilinder.

Haal de kabels door de opening van de doos voor de joystick.
Indien nodig, verwijder tijdelijk de wago's van de kabels en plaats ze daarna terug.
Plaats de doos voor de joystick op de cilinder en zorg ervoor dat de openingen van de doos zijn uitgelijnd met de holtes voorzien van moeren in de cilinder. Bevestig de doos stevig op de cilinder met 2 schroeven.

Sluit de juiste kabelschoentjes aan op de juiste schakelaars van de joystick: één voor voorwaarts samen met één voor ground, één aan de tegenoverliggende zijde voor achterwaarts samen met één voor ground, één voor links samen met één voor 5V en 1 aan de tegenoverliggende zijde voor rechts samen met één voor 5V. Zorg ervoor dat de kablschoentjes stevig vastzitten, zodat ze niet los kunnen komen. Plaats de joystick in de doos en schroef het deksel vast op de doos.

Bevestiging dashboard onderstuk

Aangespannen stuk dashboard Aangespannen stuk dashboard en joystickhouder

Bevestiging dashboard koppelstuk

Vastzetten stuurstang houder Opening voor moer stuurstang houder

Bevestiging doos joystick

Deksel met joystick Deksel voor de doos op de joystick

### Deuren en spiegels

Om de deuren te plaatsen, vijs je eerst de twee vijzen naast het dashboard uit de auto los.
 Vervolgens plaats je de deur op het auto en vijs je de twee vijzen weer door de deur en de gaatjes.
 Klik daarna de spiegels op de deuren vast, deze kunnen maar op één manier in de deur klikken.

Vastklikken spiegels Vastklikken van spiegels

### Wielen

Om de wielen te bevestigen hebben we volgend materiaal nodig: de 4 wielen, 4 velgen, 4 rondellen en 4 steekpinnen.
Maak het onderscheid tussen de voor en achterwielen, de voorwielen hebben een uitsparing in het midden terwijl de achterwielen een verhoog hebben in het midden.
Dit is duidelijk te zien op de figuur.
Draai de auto ondersteboven zodat de wielen makkelijker monteerbaar zijn. Plaats de achterwielen achteraan de auto en de voorwielen vooraan.
Schuif de achterwielen op de as van de auto, steek vervolgens de steekpin in het gat van de as.
Buig met behulp van een bektang beide benen van de steekpin, elk in een andere richting voor extra stevigheid.
Vervolgens plaatsen we de voorwielen. Plaats eerst een rondel op de as, schuif daarna het wiel op de as en plaats nog een rondel.
Het wiel mag niet los zitten, indien het wiel te los zit moet er nog een rondel bijgestoken worden.
Plaats de steekpin in het gat van de as en buig met behulp van een bektang de benen van de steekpin, elk in een andere richting voor extra stevigheid.
Als laatste klik alle velgen op de wielen. Alle velgen zijn hetzelfde dus de volgorde maakt niet uit.

Wielen Wielen en velgen

Voor en achterwielen Verschil voor en achterwielen

Auto onderkant Wielen onderkant

Bevestiging achterwiel Bevestigen achterwiel

Vastzetten achterwiel Vastzetten achterwiel met steekpin

Rondel vooras Rondel plaatsen vooras

Rondel Voorwiel Voorwiel en rondel

Vastzetten achterwiel Vastzetten voorwiel met steekpin

Velgen Velgen op wielen

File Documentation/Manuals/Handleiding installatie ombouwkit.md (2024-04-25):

# Installatie ombouwkit

<!--Hier komt in hoe ze de ombouwkit moeten installeren bij een ride on car-->

## Inhoud

<!-- Juiste volgorde bepalen wat eerst wordt gedaan -->
## Benodigdheden

Zorg dat je alle benodigdheden hebt voor je start aan het bouwen van het autootje. In die hieronder bijgevoegde lijst vind je de benodigdheden.

* Ombouwkit
* 3D-prints
* Een aantal schroevendraaiers (plat en kruis)
* Kniptang
* Striptang
* Kabelbinders
* Joystick
* Boormachine

## Installatie

### Stap 1

Koppel de kabelschoentjes los van de gaspedaal en haal de kabelschoentjes van de gaspedaal. Strip de paarse draden zodat ongeveer 1cm van de isolatie verwijderd is. Soldeer hiertussen de kill switch

Plaats de ombouwkit in de holte waar de batterij zich bevind. Stop de kabels voor de joystick in de opening waar de andere kabels lopen, respectievelijk een kabel voor links, rechts, 5V en de ground.

### Auto uitpakken

Haal de auto uit de verpakking, organiseer de inhoud per categorie en berg alle spullen netjes op om ervoor te zorgen dat er niets verloren gaat.

Uitpakken auto Auto in doos

Positioneer de auto zodanig dat de voorkant aan je rechterzijde staat. Deponeer het afval in de daarvoor bestemde vuilnisbak.  

Uitgepakte auto

### Batterij test

In de linker kant van de auto bevind zich de hoofdbekabeling van de auto. In deze bak vind je de batterij, deze is nog niet aangesloten.
 Aan de powersocket bevind er zich een rode kabel en een zwarte kabel. Sluit de rode kabel aan op het rode klepje van de batterij,
 de zwarte kabel op het zwarte klepje van de batterij. Test of de batterij goed is aangesloten door de auto aan te zetten.
 Koppel de batterij terug los nadat je deze hebt getest, zo kan er veilig gewerkt worden.  

Batterij Hoofdbekabeling

Zekering batterij Aansluiting zekering op batterij

Aangesloten batterij Aansluiting batterij

### Stuur

Het stuur dient niet bevestigd te worden op de auto gezien deze volledig vervangen wordt door een joystick.
 De joystick zal de werking van het gaspedaal en het stuur volledig over nemen.
 Bevestig de 3D prints op het dashboard, eerst dient het ronde hoge ronde stuk bevestigd te worden, dit in de inkeping van het dashboard.

> Maak de vijzen van de kabelgoot los en haal de kabelgoot van de auto.
 Zoek vervolgens de draden die naar de accelerator lopen, dit is in meeste gevallen de paarse draden. Knip deze zo dicht mogelijk door bij de accelerator.
 Knip 4 rode draden van ...cm lang en strip deze langs beide kanten. Soldeer aan 1 zijde van de draad een kabelschoen om deze dan op de joystick te kunnen schuiven.
 (kan dit loskomen door de schokken van het rijden?)
 Hang de draden aan de joystick en controleer welke draden dienen voor welke beweging, voor, achter, links of rechts. 
 Knip 1 zwarte draad van ...cm lang en strip deze langs beide kanten. Soldeer aan 1 zijde van de draad een kabelschoen om deze dan op de joystick te kunnen schuiven.
 Knip 3 korte draden van ...cm lang en strip deze langs beide kanten. Soldeer deze draden telkens tussen de ground pin van de verschillende schakelaars van de joystick.
 De draden voor de vooruit, achteruit beweging worden geschakeld tussen ?
 De draden voor de links, recht beweging worden geschakeld tussen ?
 De draad voor de ground wordt verbonden met ?

Kabelgoot Onderkant kabelgoot
Dashboard links Vijs linkerkant dashboard
Dashboard rechts Vijs rechterkant dashboard

### Kill- Switch

Om de kill-switch te plaatsen dien je eerst een gat in de achterkant van de auto te boren.
 Zorg ervoor dat het gat niet te dicht bij rand van de auto zit en dat dit makkelijk bereikbaar is aan de onderkant.  

Gat voor kill-switch

> Knip de ? draad door om hiertussen de kill-switch te plaatsen. Knip een rode en een zwarte daad van ongeveer 50cm lang, strip beide kanten van de draden.
 Soldeer beide draden aan de switch, de rode draad respectievelijk aan 1 van de buitenste pinnen van de switch, de zwarte draad aan de middelste pin.
 Vervolgens soldeer je de rode draad aan de ? kant van de doorgeknipte draad en de zwarte draad aan de ? kant. Bescherm de gesoldeerde delen met behulp van krimpkousen.
 Steek vervolgend de draad die aan de kill-switch hangt door de voorziene holte voor de achterlichten.
 Stop de kill-switch door het gat dat eerder werd gemaakt en schroef deze vast met de bijgeleverde moer.
 Om de werking van de schakelaar te testen, steek de auto aan via de on off knop. Indien de auto niet aan gaat er ergens in de schakeling een slecht contact zijn.
 Indien de auto aan gaat werkt te schakeling correct, dit kan nog eens gecontroleerd worden door de kill-switch uit te schakelen. Zo zal de auto uitvallen.

### Deuren en spiegels

Om de deuren te plaatsen vijs je eerst de twee vijzen naast het dashboard uit de auto los.
 Vervolgens plaats je de deur op het auto en vijs je de twee vijzen weer door de deur en de gaatjes.
 Klik daarna de spiegels op de deuren vast, deze kunnen maar op één manier in de deur klikken.

Vastklikken spiegels Vastklikken van spiegels

### Houder afstandsbediening

Boor een gat in de achterkant van de auto waar je de afstandsbediening wenst te plaatsen.
 Dit wordt best niet te dicht bij de kill-switch geplaatst anders verdiend deze zijn functionaliteit.
 Steek vervolgens de bout door dit gat en plaats hierop de 3D print. Bevestig dit stevig vast met de voorziene moer.
 Indien gewenst kan de print vastgezet worden met een lijmpistool voor extra stevigheid.

Houder afstandsbediening Houder voor de afstandsbediening

### Wielen

Om de wielen te bevestigen hebben we volgend materiaal nodig: de 4 wielen, 4 velgen, 4 rondellen en 4 steekpinnen.

Wielen Wielen en velgen

Maak het onderscheid tussen de voor en achterwielen, de voorwielen hebben een uitsparing in het midden terwijl de achterwielen een verhoog hebben in het midden.
 Dit is duidelijk te zien op de figuur.
 Draai de auto ondersteboven zodat de wielen makkelijker monteerbaar zijn. Plaats de achterwielen achteraan de auto en de voorwielen vooraan.

Voor en achterwielen Verschil voor en achterwielen
Auto onderkant Wielen onderkant

Schuif de achterwielen op de as van de auto, steek vervolgens de steekpin in het gat van de as.
 Buig met behulp van een bektang beide benen van de steekpin, elk in een andere richting voor extra stevigheid.

Bevestiging achterwiel Bevestigen achterwiel
Vastzetten achterwiel Vastzetten achterwiel met steekpin

Vervolgens plaatsen we de voorwielen. Plaats eerst een rondel op de as, schuif daarna het wiel op de as en plaats nog een rondel.
 Het wiel mag niet los zitten, indien het wiel te los zit moet er nog een rondel bijgestoken worden.
 Plaats de steekpin in het gat van de as en buig met behulp van een bektang de benen van de steekpin, elk in een andere richting voor extra stevigheid.

Rondel vooras Rondel plaatsen vooras
Rondel Voorwiel Voorwiel en rondel
Vastzetten achterwiel Vastzetten voorwiel met steekpin

Als laatste klik alle velgen op de wielen. Alle velgen zijn hetzelfde dus de volgorde maakt niet uit.

Velgen Velgen op wielen

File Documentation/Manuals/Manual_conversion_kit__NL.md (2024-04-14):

# Handleiding ombouwkit

## inhoud

<!-- Juiste volgorde bepalen wat eerst wordt gedaan -->
## Benodigdheden

Zorg dat je alle benodigdheden hebt voor je start aan het bouwen van het autootje. In die hieronder bijgevoegde lijst vind je de benodigdheden.

* Een aantal schroevendraaiers (plat en kruis)
* Kniptang
* Lijmpistool + lijm
* Striptang
* Pop rivet tang + Poprivetten
* Bektang
* Kabels
* Krimpkous
* Soldeertin
* Kabelbinders
* Wago's
* Joystick
* Lusterklem
* Kabelschoen
* Soldeerbout
* Boormachine

## Aanpassing

### Auto uitpakken

Haal de auto uit de verpakking, organiseer de inhoud per categorie en berg alle spullen netjes op om ervoor te zorgen dat er niets verloren gaat.

Uitpakken auto Auto in doos

Positioneer de auto zodanig dat de voorkant aan je rechterzijde staat. Deponeer het afval in de daarvoor bestemde vuilnisbak.  

Uitgepakte auto

### Batterij test

In de linker kant van de auto bevind zich de hoofdbekabeling van de auto. In deze bak vind je de batterij, deze is nog niet aangesloten.
 Aan de powersocket bevind er zich een rode kabel en een zwarte kabel. Sluit de rode kabel aan op het rode klepje van de batterij,
 de zwarte kabel op het zwarte klepje van de batterij. Test of de batterij goed is aangesloten door de auto aan te zetten.
 Koppel de batterij terug los nadat je deze hebt getest, zo kan er veilig gewerkt worden.  

Batterij Hoofdbekabeling

Zekering batterij Aansluiting zekering op batterij

Aangesloten batterij Aansluiting batterij

### Stuur

Het stuur dient niet bevestigd te worden op de auto gezien deze volledig vervangen wordt door een joystick.
 De joystick zal de werking van het gaspedaal en het stuur volledig over nemen.
 Bevestig de 3D prints op het dashboard, eerst dient het ronde hoge ronde stuk bevestigd te worden, dit in de inkeping van het dashboard.

> Maak de vijzen van de kabelgoot los en haal de kabelgoot van de auto.
 Zoek vervolgens de draden die naar de accelerator lopen, dit is in meeste gevallen de paarse draden. Knip deze zo dicht mogelijk door bij de accelerator.
 Knip 4 rode draden van ...cm lang en strip deze langs beide kanten. Soldeer aan 1 zijde van de draad een kabelschoen om deze dan op de joystick te kunnen schuiven.
 (kan dit loskomen door de schokken van het rijden?)
 Hang de draden aan de joystick en controleer welke draden dienen voor welke beweging, voor, achter, links of rechts. 
 Knip 1 zwarte draad van ...cm lang en strip deze langs beide kanten. Soldeer aan 1 zijde van de draad een kabelschoen om deze dan op de joystick te kunnen schuiven.
 Knip 3 korte draden van ...cm lang en strip deze langs beide kanten. Soldeer deze draden telkens tussen de ground pin van de verschillende schakelaars van de joystick.
 De draden voor de vooruit, achteruit beweging worden geschakeld tussen ?
 De draden voor de links, recht beweging worden geschakeld tussen ?
 De draad voor de ground wordt verbonden met ?

Kabelgoot Onderkant kabelgoot
Dashboard links Vijs linkerkant dashboard
Dashboard rechts Vijs rechterkant dashboard

### Kill- Switch

Om de kill-switch te plaatsen dien je eerst een gat in de achterkant van de auto te boren.
 Zorg ervoor dat het gat niet te dicht bij rand van de auto zit en dat dit makkelijk bereikbaar is aan de onderkant.  

Gat voor kill-switch

> Knip de ? draad door om hiertussen de kill-switch te plaatsen. Knip een rode en een zwarte daad van ongeveer 50cm lang, strip beide kanten van de draden.
 Soldeer beide draden aan de switch, de rode draad respectievelijk aan 1 van de buitenste pinnen van de switch, de zwarte draad aan de middelste pin.
 Vervolgens soldeer je de rode draad aan de ? kant van de doorgeknipte draad en de zwarte draad aan de ? kant. Bescherm de gesoldeerde delen met behulp van krimpkousen.
 Steek vervolgend de draad die aan de kill-switch hangt door de voorziene holte voor de achterlichten.
 Stop de kill-switch door het gat dat eerder werd gemaakt en schroef deze vast met de bijgeleverde moer.
 Om de werking van de schakelaar te testen, steek de auto aan via de on off knop. Indien de auto niet aan gaat er ergens in de schakeling een slecht contact zijn.
 Indien de auto aan gaat werkt te schakeling correct, dit kan nog eens gecontroleerd worden door de kill-switch uit te schakelen. Zo zal de auto uitvallen.

### Deuren en spiegels

Om de deuren te plaatsen vijs je eerst de twee vijzen naast het dashboard uit de auto los.
 Vervolgens plaats je de deur op het auto en vijs je de twee vijzen weer door de deur en de gaatjes.
 Klik daarna de spiegels op de deuren vast, deze kunnen maar op één manier in de deur klikken.

Vastklikken spiegels Vastklikken van spiegels

### Houder afstandsbediening

Boor een gat in de achterkant van de auto waar je de afstandsbediening wenst te plaatsen.
 Dit wordt best niet te dicht bij de kill-switch geplaatst anders verdiend deze zijn functionaliteit.
 Steek vervolgens de bout door dit gat en plaats hierop de 3D print. Bevestig dit stevig vast met de voorziene moer.
 Indien gewenst kan de print vastgezet worden met een lijmpistool voor extra stevigheid.

Houder afstandsbediening Houder voor de afstandsbediening

### Wielen

Om de wielen te bevestigen hebben we volgend materiaal nodig: de 4 wielen, 4 velgen, 4 rondellen en 4 steekpinnen.

Wielen Wielen en velgen

Maak het onderscheid tussen de voor en achterwielen, de voorwielen hebben een uitsparing in het midden terwijl de achterwielen een verhoog hebben in het midden.
 Dit is duidelijk te zien op de figuur.
 Draai de auto ondersteboven zodat de wielen makkelijker monteerbaar zijn. Plaats de achterwielen achteraan de auto en de voorwielen vooraan.

Voor en achterwielen Verschil voor en achterwielen
Auto onderkant Wielen onderkant

Schuif de achterwielen op de as van de auto, steek vervolgens de steekpin in het gat van de as.
 Buig met behulp van een bektang beide benen van de steekpin, elk in een andere richting voor extra stevigheid.

Bevestiging achterwiel Bevestigen achterwiel
Vastzetten achterwiel Vastzetten achterwiel met steekpin

Vervolgens plaatsen we de voorwielen. Plaats eerst een rondel op de as, schuif daarna het wiel op de as en plaats nog een rondel.
 Het wiel mag niet los zitten, indien het wiel te los zit moet er nog een rondel bijgestoken worden.
 Plaats de steekpin in het gat van de as en buig met behulp van een bektang de benen van de steekpin, elk in een andere richting voor extra stevigheid.

Rondel vooras Rondel plaatsen vooras
Rondel Voorwiel Voorwiel en rondel
Vastzetten achterwiel Vastzetten voorwiel met steekpin

Als laatste klik alle velgen op de wielen. Alle velgen zijn hetzelfde dus de volgorde maakt niet uit.

Velgen Velgen op wielen

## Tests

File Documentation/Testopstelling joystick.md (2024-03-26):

# Testing joystick

Er werd een testopstelling gemaakt met de digitale joystick om deze te testen op werking. De verschillende schakelaars werden gecontroleerd. Dit gebeurde aan de hand van het aansturen van LED's die parallel werden geschakeld met de joystick.

De joystick werd aangestuurd met een generator (Keysight EDU 34450 Toestel nummer 10) die ingesteld werd op 12V. Er werd eveneens een multimeter (Keysight EDU 34450 Toetel nummer 10) gebruikt om de spanning over de schakeling te meten.
Elke LED werd voorzien van een weerstand met een weerstandswaarde van 560 ohm om de LED's te beschermen.

In dit filmpje is de testopstelling te zien en de werking van de joystick.

https://github.com/vives-project-xp/GoBabyGo2.1/assets/140738348/114d1432-ddc6-4e2f-8776-aefe02c559a6

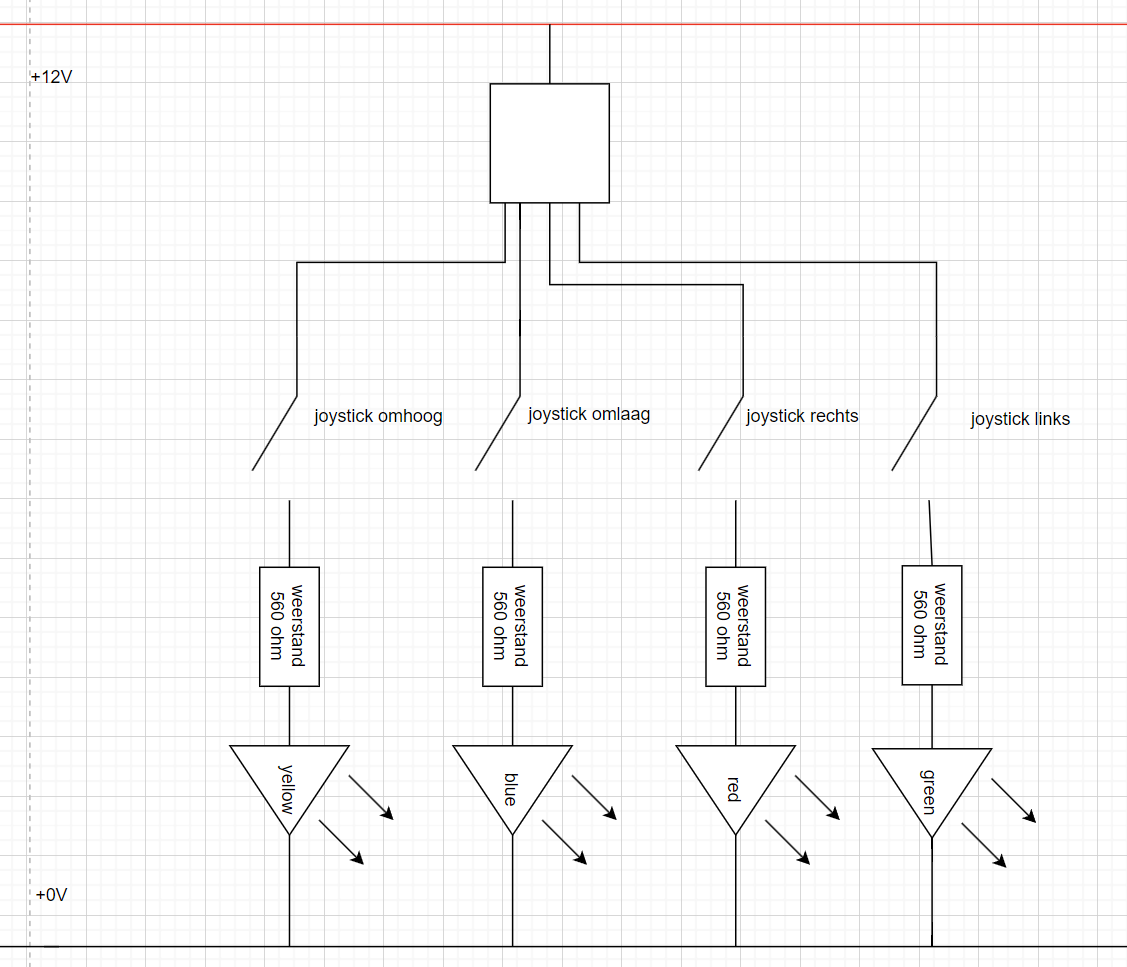
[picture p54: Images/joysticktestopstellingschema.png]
joysticktestopstelling schema joystick testopstelling


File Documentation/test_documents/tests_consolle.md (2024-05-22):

# motor testen
Om de werking te testen va, de verschillende motoren in de auto, is het mogelijk om de verschillende spanningen te meten op de aansluitpinnen van de motordrivers. In het geval van de voorwaardse en achterwaards beweging kan er gemeten worden op de moordriver die is meegeleverd et de auto. Deze driver stuurt de 2 motoren aan die aan de achterkant van de auto te vinden zijn.

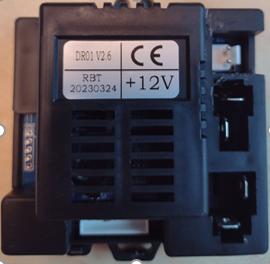
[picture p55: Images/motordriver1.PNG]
motordriver1 motordriver meegeleverd met de auto


Hieronder zijn de verwachte waarden en de gemeten waarden te zien van de spanningen die over de motoren zouden komen
### verwachtingen
tests|Motor|opmerkingen
:---------------------|:------|:----------------------------------------------
joystick forward | 12V | motoren gaan vooruit
joystick backwards | -12V | motoren gaan achteruit
||
controller forward | 12V | motoren gaan vooruit
controller backwards | -12V | motoren gaan achteruit

### metingen
tests|Motor|opmerkingen
:---------------------|:------|:----------------------------------------------
joystick forward | 12,78V | motoren gaan vooruit
joystick backwards | -12,81V | motoren gaan achteruit
||
controller forward | 12,75V | motoren gaan vooruit
controller backwards | -12,77V | motoren gaan achteruit

Voor de stuurbeweging hebben we een extra motordriver moeten toevoegen aangezien deze beweging normaal gedaan werd door het draaien van het stuur. Er wordt nu gebruik gemaakt van de L298N motordriver, voor de sturing met de joystick, aangezien deze werd gebruikt in het project 'GoBabyGo 2.0' en werkt op 12V die geleverd wordt door de batterij. Door het gebruik van een extra motordriver is er een kleine spanningsval op de uitgang waar de stuurmotor aan verbonde wordt.

Wanneer we gebruik maken van een relais is het mogelijk om de 2 motordrivers te combineren. Op die manier kan gestuurd worden met de joystick en de afstandsbediening waar de 2de optie de voorang krijgt.

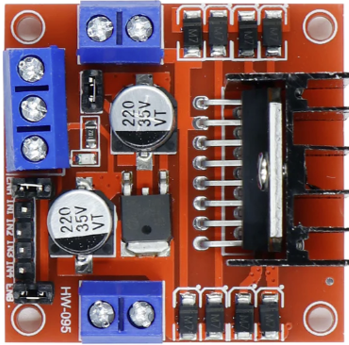
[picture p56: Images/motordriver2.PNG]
motordriver1 extra motordriver


Hieronder zijn de verwachte waarden en de gemeten waarden te zien van de spanningen die over de motor zou komen
### expectations
tests|Motor|opmerkingen
:---------------------|:------|:----------------------------------------------
joystick left | 7,4V | stuur links
joystick right | -7,4V | stuur rechts
||
controller left | 12V | stuur links
controller right | -12V | stuur rechts
### metingen
tests|Motor|opmerkingen
:---------------------|:------|:----------------------------------------------
joystick left | 8,1V | stuur links
joystick right | -7,95V  | stuur rechts
||
controller left | / | stuur links
controller right | / | stuur rechts

De reden waarom alle metingen hoger zijn dan de verwachte waarde is de spanning van de batterij. Normaal zou deze 12V moten zijn maar na het meten is deze 12,84V

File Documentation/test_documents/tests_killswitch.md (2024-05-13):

## expectations

test|killswitch state|results|comments
:----------------|:----------------:|:----------------:|:----------------
forward| 0 | 0 | do nothing
backward| 0 | 0 | do nothing
left| 0 | 1 | steer to the left
right| 0 | 1 | steer to the right
| | |
| | |
forward| 1 | 1 | driver forward
backward| 1 | 1 | driver backwards
left| 1 | 1 | steer to the left
right| 1 | 1 | steer to the right

## test killswitch

test|killswitch state|results|comments
:----------------|:----------------:|:----------------:|:----------------
forward| 0 | 0 | Is disabled
backward| 0 | 0 | Is disabled
left| 0 | 1 | Still works
right| 0 | 1| Still works
| | |
| | |
forward| 1 | 1| Drive forward
backward| 1 | 1 | Drive backwards
left| 1 | 1 | Steer left
right| 1 | 1 | Steer right

## Extra Comments:

No matter what state the kill switch is in the left or right steering still works.
This is no problem as you can't move forward or backward so you can't move at all when the switch isn't active.

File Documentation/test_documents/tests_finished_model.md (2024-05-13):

#tests protoypt

tests|results|comments|
:-----------------------------------------------------------|:----------------:|:----------------------------------------------------------------
kill switch stops forward and backward movement| Yes | If the killswitch is turned off the car can only turn right/left wich doesn't do anything because the fwd bwk doesnt work in that state.
powerbotton stops total working from the car| Yes | We didn't change this from the original car design.
batery can be charged no matter the state of anny switches| Yes | We didn't change this from the original car design.
the car cant be driver while charfing| Yes | We didn't change this from the original car design. The powerplug has already this feature installed.
| | |
| | |
drive forward with joystick| Yes | Works perfectly.
drive backwards with joystick| Yes | Works perfectly. 
turn left with joystick| Yes | Works perfectly.
turn right with joystick| Yes | Works perfectly.
| | |
| | |
drive forward right with joystick| Yes | Works perfectly.
driver forward left with joystick| Yes | Works perfectly.
drive backwards right with joystick| Yes | Works perfectly.
drive backwards left with joystick| Yes | Works perfectly.
| | |
| | |
drive forward with controller| Yes |  We didn't change this from the original car design. 
drive backwards with controller| Yes |  We didn't change this from the original car design. 
turn left with controller| No | Relais didn't arrive yet so this couldn't be tested in time.
turn right with controller| No | Relais didn't arrive yet so this couldn't be tested in time. 
| | |
| | |
drive forward right with controller| No | Relais didn't arrive yet so this couldn't be tested in time.
driver forward left with controller| No | Relais didn't arrive yet so this couldn't be tested in time.
drive backwards right with controller| No | Relais didn't arrive yet so this couldn't be tested in time.
drive backwards left with controller| No | Relais didn't arrive yet so this couldn't be tested in time. 
| | |
| | |
controller overruled joystick forward/backward| Yes | We didn't change this from the original car design. 
controller overruled joystick left/right| Should work in Theory  | Relais didn't arrive yet so this couldn't be tested in time.

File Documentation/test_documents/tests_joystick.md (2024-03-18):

## tests joystick

tests|M1 pin 1|M1 pin2|M2 pin1|M2 pin2|M3 pin 1|M3 pin2|comments
:-----------|:-------:|:-------:|:-------:|:-------:|:-------:|:-------:|:------------------------------------------------------
forward|  |  |  |  |  |  |  
backward|  |  |  |  |  |  |  
left| _ | _ | _ | _ | _ | _ | _ 
right| _ | _ | _ | _ | _ | _ | _ 

## expectations

tests|M1 pin 1|M1 pin2|M2 pin1|M2 pin2|M3 pin 1|M3 pin2|comments
:-----------|:-------:|:-------:|:-------:|:-------:|:-------:|:-------:|:------------------------------------------------------
forward| 12V | 0V | 0V | 12V | / | / | drive forward
backward| 0V | 12V | 12V | 0V | / | / | driver backwards
left| / | / | / | / | 12V | 0V | steer to the left
right| / | / | / | / | 0V | 12V | steer to the right

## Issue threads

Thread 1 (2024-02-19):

Gesprek De Beule Isabelle

LynnDelaere, 2024-02-19:
Er wordt een gesprek georganiseerd met Mevr. Isabelle De Beule van zorgtechnologie om info in te winnen over het project en hun verwachtingen. De vergadering die we gehad hebben werd uitgetypt, met vraag en antwoord.

LynnDelaere, 2024-02-19:
[VragenIsabelDeBeule.docx](https://github.com/vives-project-xp/GoBabyGo2.1/files/14334407/VragenIsabelDeBeule.docx)

Closed 2024-02-26.

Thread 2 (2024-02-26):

Testen Digitale Joystick

LynnDelaere, 2024-02-26:
Er werd een schakeling gemaakt om de werking van de digitale joystick uit te testen. Dit werd uitgevoerd op een breadboard met een LED schakeling.
Dit ter vervanging van de ESP32.
De joystick dient om een hoog of laag signaal door te sturen naar de motoren en deze aan te sturen.
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

LynnDelaere, 2024-02-26:
https://github.com/vives-project-xp/GoBabyGo2.1/assets/140738348/9726726b-3386-4fa6-9474-e58acd85a3d1

LynnDelaere, 2024-03-04:
Documentatie aangemaakt testopstelling

Closed 2024-03-07.

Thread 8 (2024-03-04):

Ombouwkit

LynnDelaere, 2024-03-04:
File aangemaakt om documentatie bij te houden voor de ombouwkit

bavolezy, 2024-03-18:
gaat da nie beter en gemakkelijker zijn als we handleiding parallel maken met de auto.
dus dawe een auto from scratch kunnen opvolgen foto's trekken en noteren wat te doen, dat zal dan ook preciezer zijn

LynnDelaere, 2024-04-14:
ombouwkit wordt aangepast zodat er een Engelse en Nederlandse versie is voor het bevestigen van de joystick. Er wordt een handleiding gemaakt voor de ouders.

LynnDelaere, 2024-04-29:
Document opgesteld en uitgetypt met uitleg hoe de ombouwkit moet gemaakt worden

Closed 2024-05-09.

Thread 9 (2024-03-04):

Bezoek ouders

LynnDelaere, 2024-03-04:
Lieve Debackere is vandaag langs gekomen. Er is een kindje die in aanmerking komt voor een aangepaste auto met joystick.
Samen met de ouders wordt er gekeken naar een geschikte datum om samen te komen.
Lieve wordt op de hoogte gehouden van de stand van zaken.

LynnDelaere, 2024-03-07:
Aftoetsen of het voor iedereen mogelijk is om naar Moorsele te geraken om eens af te spreken met de ouders

LynnDelaere, 2024-03-11:
Mail gestuurd naar Lieve dat dit voor ons in het weekend enkel de zondag past en anders in de week als dit in ons uurrooster past.

LynnDelaere, 2024-04-14:
Bezoek ouders staat gepland op 15/04 rond 15u30. Misschien is er die dag een mogelijkheid dat Victor de auto al kan testen met de joystick.

LynnDelaere, 2024-04-29:
Bezoek ouders is geweest en er werd een verslag uitgetypt met opmerkingen

Closed 2024-04-29.

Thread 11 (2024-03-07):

3D prints

LynnDelaere, 2024-03-07:
Er werden 3D prints getekend om de joystick te bevestigen ipv het stuur waarbij er gezorgd wordt dat de stuurstang niet zakt zodat de links rechts beweging nog kan uitgevoerd worden. De 3D prints zijn echter niet in het juiste formaat getekend.

LynnDelaere, 2024-03-11:
3D prints werden aangepast en opnieuw ingegeven

AlberiekDepreytere, 2024-03-25:
3D prints print structuur verwijderen + schuren voor vlotte doorgang van de kabels.
Moeren bevestigen in de Print.

Scherpe hoeken vermijden en test monteren om een goeie werking te garanderen.

25/03 van 8:20 tot 10:10

LynnDelaere, 2024-04-29:
3D prints werden geüpload in documentatie

Closed 2024-04-29.

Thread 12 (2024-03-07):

Testen Joystick met auto

LynnDelaere, 2024-03-07:
Eens we een oplossing gevonden hebben voor de verbinding met de motordriver en de hardware aanwezig is voor deze verbinding. Kan de joystick getest worden met de auto

AlberiekDepreytere, 2024-03-25:
Monteren van de Joystick in de auto + werking controleren.
Conclusie werkt naar behoren (Onderstuk 3D print nog eens herbevestigen.

(Overriden nog eens controleren.) Middag van 25/03 14:00 tot  20:00.

AlberiekDepreytere, 2024-05-13:
Werkt naar behoren ook wanneer alles is aangesloten. getest en laatste volledige controle op 06/05.

AlberiekDepreytere, 2024-05-13:
.

Closed 2024-05-13.

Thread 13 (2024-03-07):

Bestellijst

LynnDelaere, 2024-03-07:

LynnDelaere, 2024-03-07:
Het nodige materiaal werd aan de bestellijst toegevoegd

LynnDelaere, 2024-03-07:
Nog te bestellen materiaal voor verbinding tussen motor driver, joystick en controler

LynnDelaere, 2024-03-07:
3D print moet opnieuw getekend worden voor de bestellijst maar Lynn kan dit eventueel thuis printen

LynnDelaere, 2024-03-11:
Stroom door kill switch gemeten, deze is 70mA. De switch die gekozen werd is in orde

LynnDelaere, 2024-04-15:
Regelbare step-down en motordriver op bestellijst geplaatst

LynnDelaere, 2024-04-29:
Al het nodige werd besteld en geleverd

Closed 2024-04-29.

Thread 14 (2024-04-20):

Onstabiele ombouw 3D prints

LynnDelaere, 2024-04-20:
Tijdens het bezoek van Viktor merkte we tijdens de beweging van de joystick de 3D prints wat mee gingen met de beweging. Hierdoor was het voor Viktor moeilijker om de auto te besturen.
Er wordt gewerkt aan een beter 3D design die dit zou moeten voorkomen.

LynnDelaere, 2024-04-29:
3D prints aangepast en stabiliteit is verbeterd

Closed 2024-04-29.

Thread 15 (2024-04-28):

Pers bericht

LynnDelaere, 2024-04-28:
Er werd contact opgenomen met Hannelore Crijns met de vraag of het mogelijk was om de pers te contacteren zodat ze op 15mei kunnen langs komen om ons project voor te stellen tijdens de drive in van zorgtechnologie.

LynnDelaere, 2024-04-29:
Lieve Debackere heeft Hannelore Crijns extra informatie verschaft over de Drive in van 15 mei

LynnDelaere, 2024-04-29:
Hannelore gaat aan de slag om een pers bericht te schrijven en zal dit begin volgende week doorsturen naar ons

Closed 2024-05-09.

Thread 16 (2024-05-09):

Foto's ombouwkit

LynnDelaere, 2024-05-09:
nog een foto te maken van de motordriver in de grijze auto met de correcte bekabeling

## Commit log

2024-03-04 3D prints
    [joystick.stl, joystickhouder.stl, joystickhouderhouder.stl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]
2024-03-04 stl files
    [joystickhouder.stl, joystickhouderhouder.stl, stanghouder.stl]
2024-03-11 3D print size changed
    [joystick.3mf, joystick.stl, joystickhouder.3mf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]
2024-03-18 3D prints aangepast
    [joystick.3mf, joystickhouder.3mf, joystickhouderhouder.3mf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]
2024-04-20 link 3D prints map
2024-04-20 3D prints verplaatst
    [joystick.3mf, joystickhouder.3mf, joystickhouderhouder.3mf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]
2024-04-24 Aanpassing ombouwkit
    [doze v6.3mf, joystick assembly v9.3mf, steurstangevastzetter v1.3mf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]
2024-04-24 Final 3D prints
    [Assembly.3mf, DashboardKoppelstuk.3mf, DashboardOnderstuk.3mf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]
2024-04-24 Foto's 3D-prints joystick added
2024-04-24 Foto's toegevoegd verbinding motordriver
2024-04-29 Foto 5V kabel toegevoegd
2024-04-29 Bekabeling ground aangepast
2024-05-01 Aanpassing Kill-switch
2024-05-09 Final 3D prints toegevoegd
    [Assembly.3mf, DashboardKoppelstuk.3mf, DashboardOnderstuk.3mf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]
2024-05-09 Aanpassing naam folder
    [joystick.3mf, joystickhouder.3mf, joystickhouderhouder.3mf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]
2024-05-12 Aanpassing joystick en 3D prints uitwerking
2024-05-12 Aanpassing 3D-prints joystick
2024-05-13 Verwijderen foto ground bekabeling
